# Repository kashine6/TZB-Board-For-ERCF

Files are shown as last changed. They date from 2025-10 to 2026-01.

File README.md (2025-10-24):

# TZB V1 Mainboard Manual

English | [中文](README_CN.md)

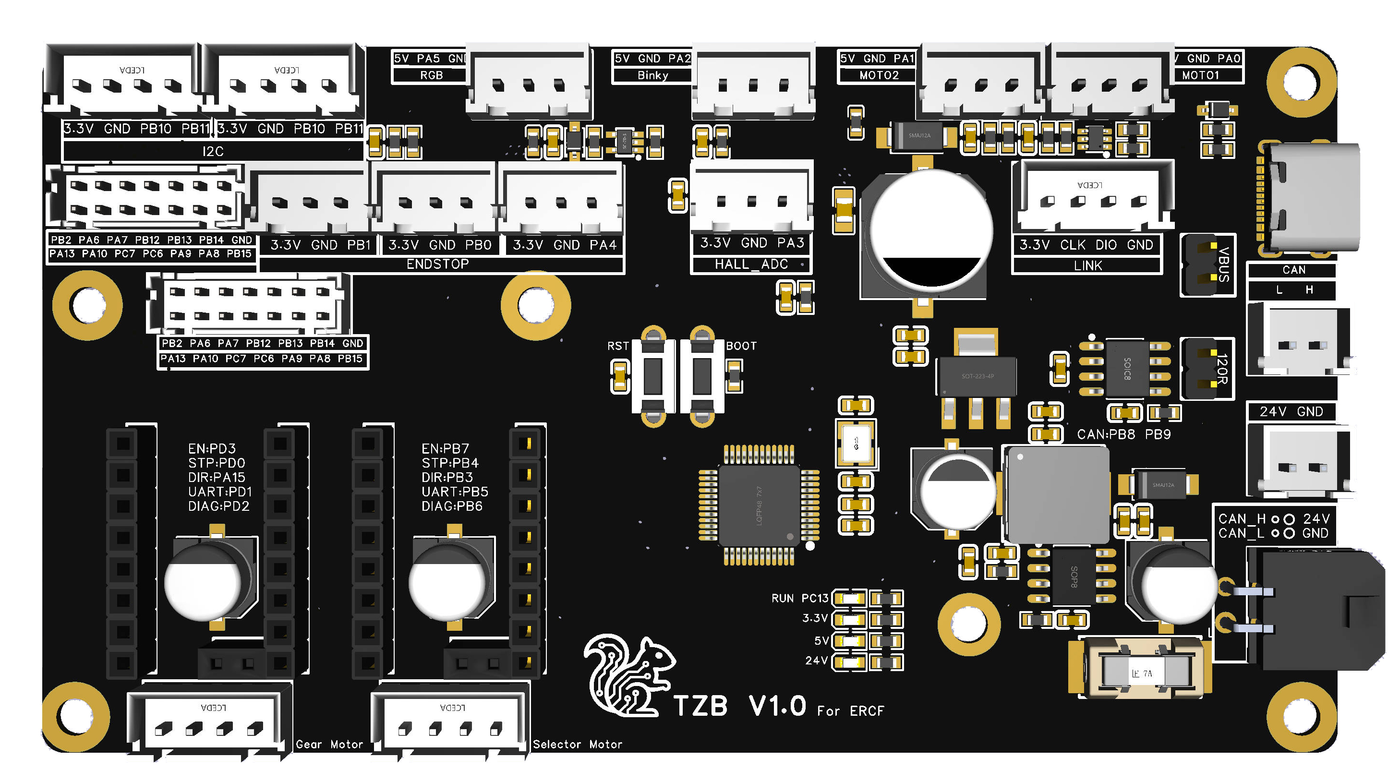
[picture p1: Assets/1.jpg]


---

## Table of Contents

- [1. Introduction](#1-introduction)
- [2. PIN Diagram](#2-pin-diagram)
- [3. Flashing Guide](#3-flashing-guide)
  - [3.1. Flashing Katapult (Optional)](#31-flashing-katapult-optional)
  - [3.2. Compiling Klipper Firmware](#32-compiling-klipper-firmware)
  - [3.3. Updating Firmware via Katapult](#33-updating-firmware-via-katapult)
  - [3.4. Updating Firmware via DFU](#34-updating-firmware-via-dfu)
- [4. ERCF Wiring Diagram](#4-ercf-wiring-diagram)
- [5. Happy Hare Software Configuration](#5-happy-hare-software-configuration)
- [6. I2C Temperature and Humidity Configuration](#6-i2c-temperature-and-humidity-configuration)

---

## 1. Introduction

The **TZB V1 Mainboard** is a dedicated mainboard developed for the ERCF.

It has the following features:

- Main chip uses STM32G0B1CBT6 MCU
- Supports both USB serial and CAN interface connections
- 2 stepper motor slots based on TMC2209 in UART mode, supporting sensorless homing (Diag)
- The 5V interface can provide a large current of 5A, with optimized inductor and capacitor heat dissipation to ensure sufficient and stable power for servos and LEDs
- Two mirrored 2x7P XHD2.0 connectors, convenient for paralleling the two sets of microswitches in ERCF V3, simplifying wiring
- All silkscreen labels are on the front for ease of use
- 1 x RGB LED connector
- 2 x Servo connectors, capable of driving a remote cutters
- 1 x Binky encoder connector
- 16 x Microswitch control connectors, which can support up to a 16-color ERCF if fully utilized
- 1 x I2C interface, using a hardware I2C port, which can be used to connect a temperature and humidity sensor
- 1 x 24V GND connector, which can be used to supply power to remote cutters that require more than 5V
- 1 x External CAN connector, which can be used to connect other mainboards, such as a passive enclosure mainboard
- 1 x ADC interface, for use with a proportional filament sync feedback sensor using an analog Hall effect sensor

## 2. PIN Diagram

The wiring diagram for this mainboard is entirely on the front, making it clear at a glance without needing a separate pinout diagram.



## 3. Flashing Guide

### 3.1 Flashing Katapult (Optional)

Users who only use a CAN connection and want the convenience of quick firmware updates by pressing the Reset button can choose to flash Katapult (formerly known as Canboot).

Katapult is not mandatory, regardless of whether you use a CAN or USB connection.

```bash
# Go to the home directory
cd ~
 
# Download katapult (skip if you already have it)
git clone https://github.com/Arksine/katapult
 
# Enter the katapult directory
cd katapult
```

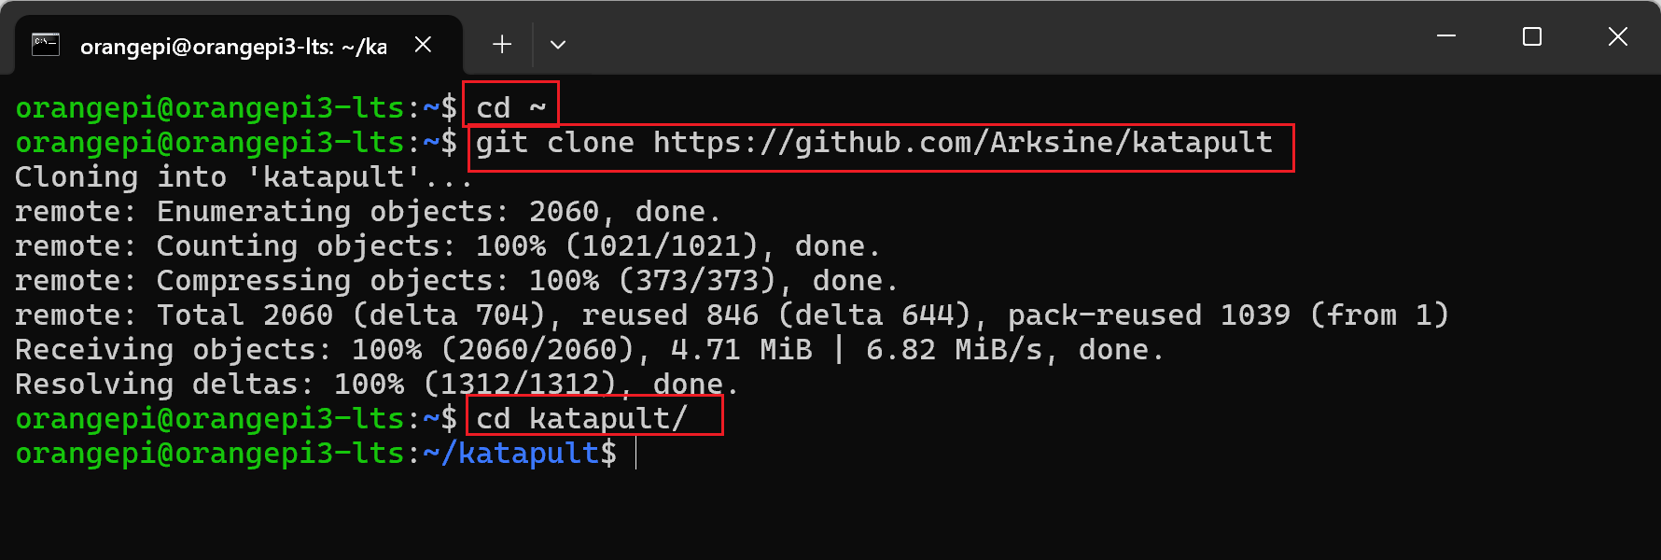
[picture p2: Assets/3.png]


```bash
# Clean the previous build
make clean
 
# Modify the build configuration, fill in the parameters as shown in the image below
make menuconfig
 
# After verifying the settings, press q to exit, select y, then type make to start compiling
make
```

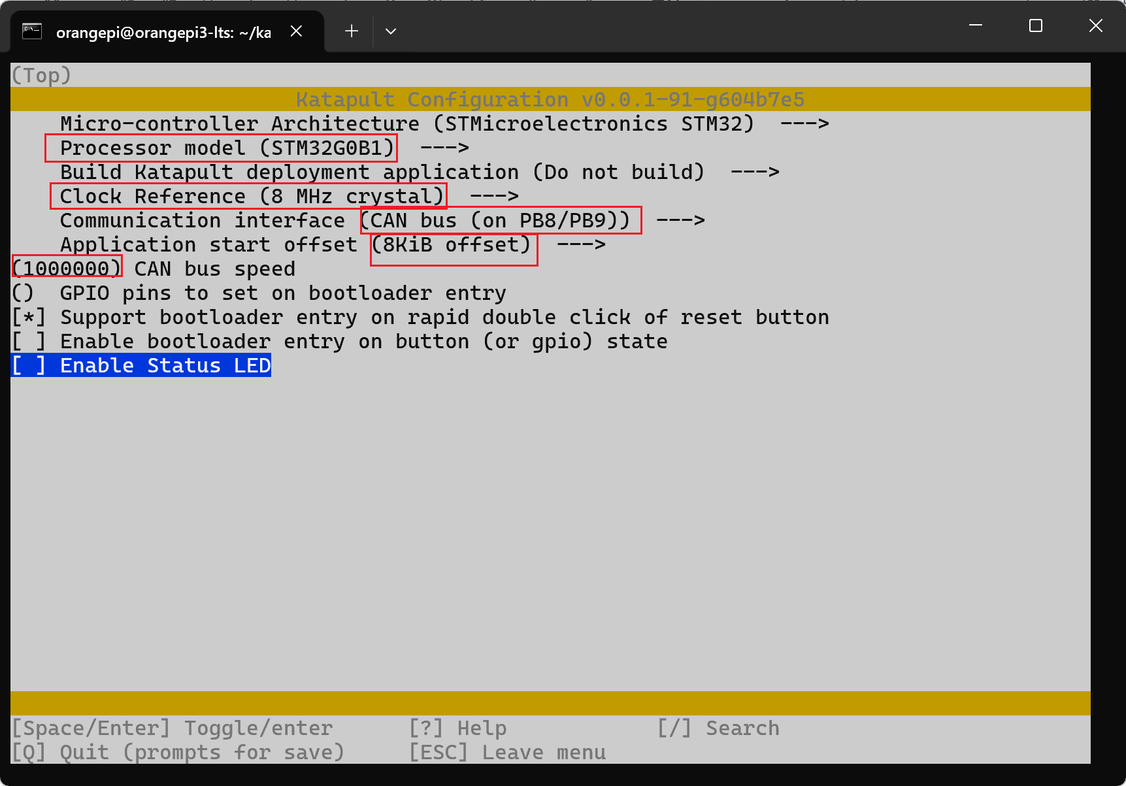
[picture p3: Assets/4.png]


> [!TIP]
> The speed can be set according to your needs, 1000000 is recommended.

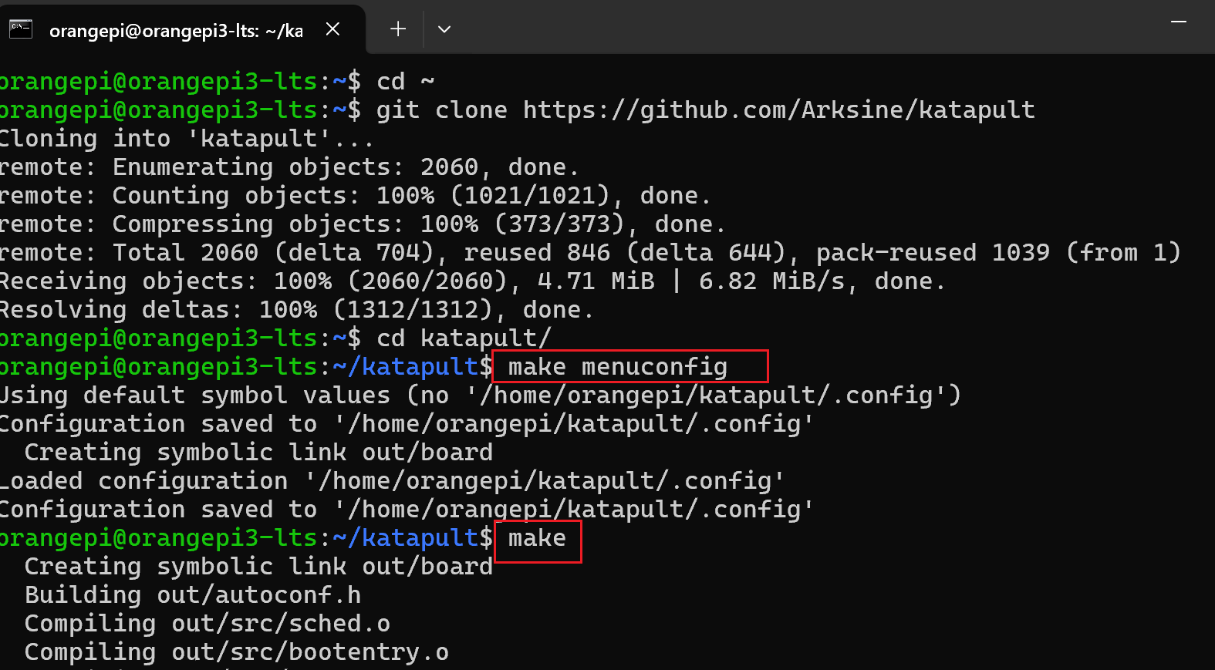
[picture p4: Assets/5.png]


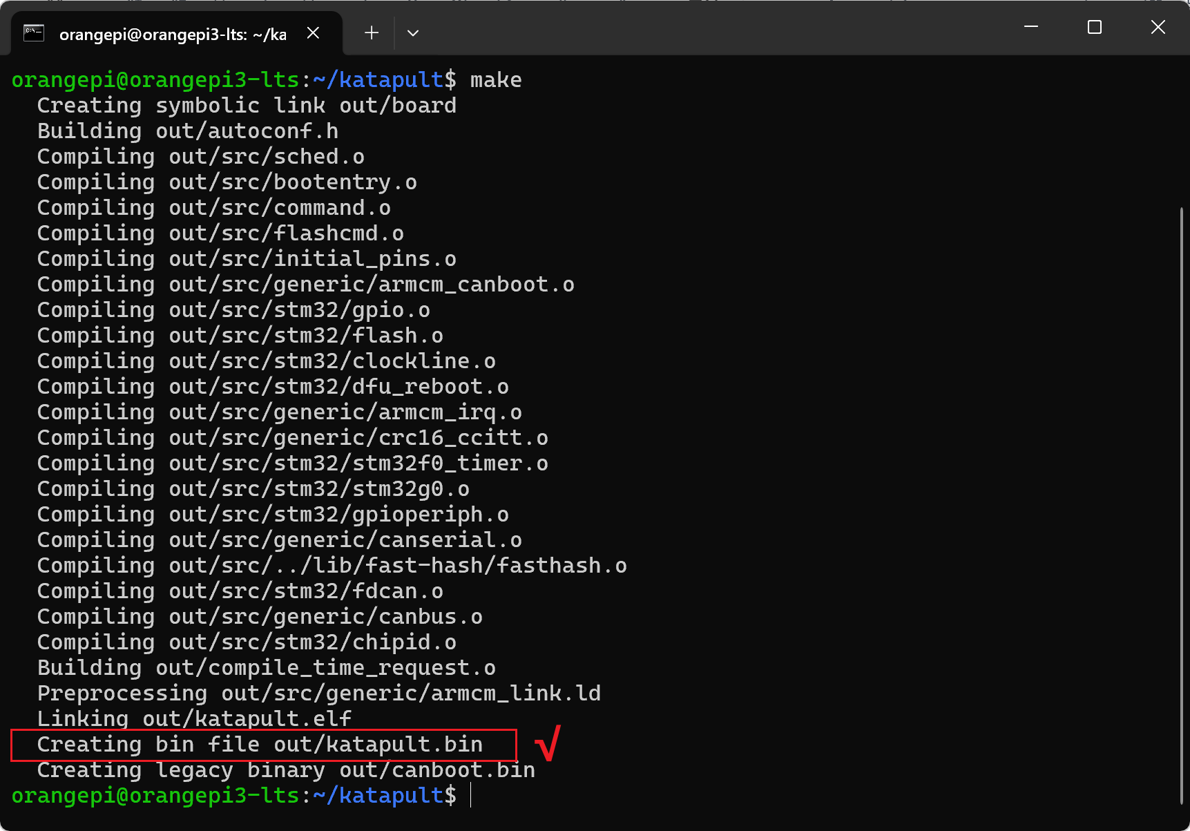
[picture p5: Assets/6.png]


After compilation, katapult.bin will be generated in the ~/katapult/out folder.

**Entering DFU Mode**

Use a jumper to short the 5V USB pins. After shorting, you can power the board via USB for flashing. 

> [!TIP]
> Remember to remove the jumper after flashing is complete.  

If you are using 24V to power the board, you do not need to short the jumper, but you can only use Method 2 below to enter DFU mode.

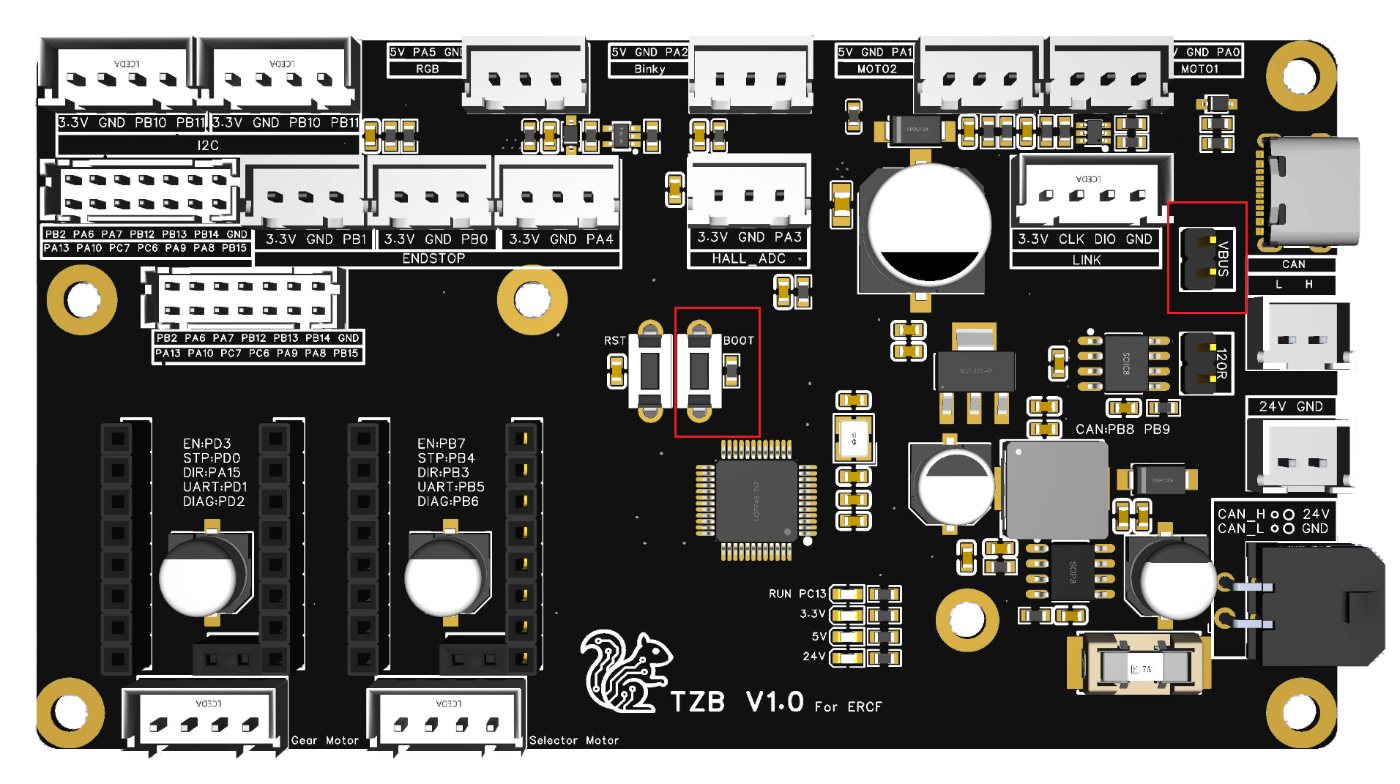
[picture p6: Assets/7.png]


- **Method 1 to enter DFU:** With the board completely powered off, press and hold the Boot button, connect the board to the host computer with a Type-C cable, then release the Boot button.

- **Method 2 to enter DFU:** If the board is powered on, connect it to the host computer with a Type-C cable, then press and hold the Boot button, press and release the Reset button, release the Reset button, and finally release the Boot button.

Then use the lsusb command to check if a DFU device is present.

```bash
lsusb
```

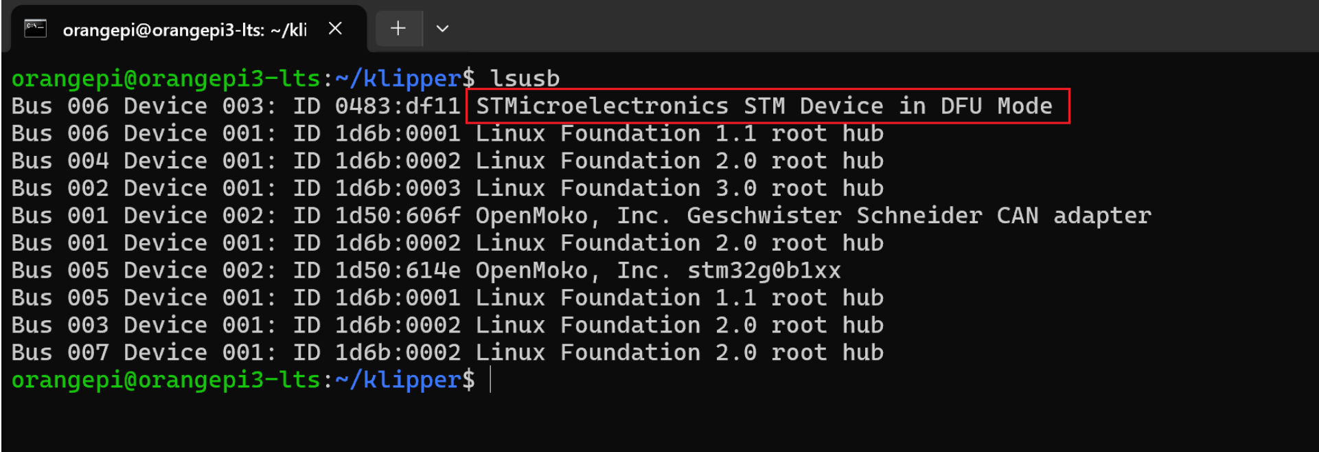
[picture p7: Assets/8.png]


Use the following command to flash the board:

```bash
make flash FLASH_DEVICE=0483:df11
```

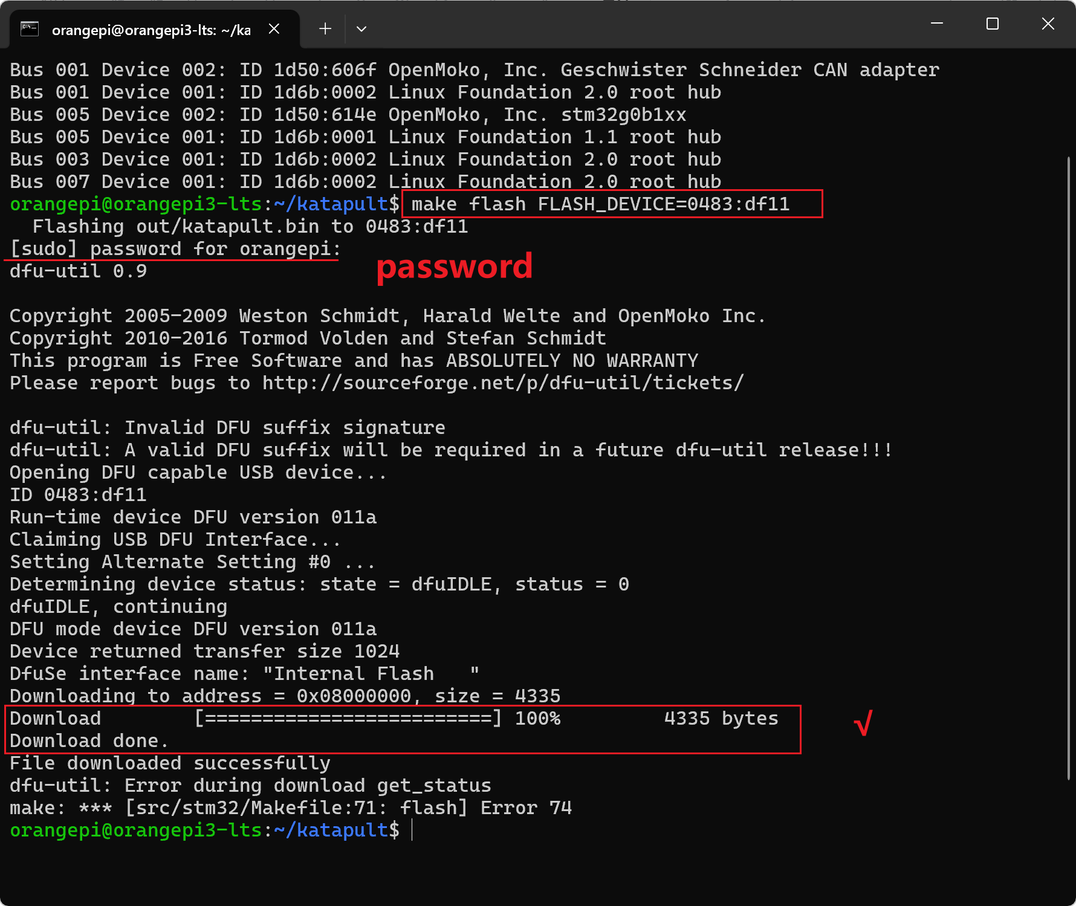
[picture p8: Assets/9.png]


After flashing is complete, please unplug the USB cable and connect the CAN signal cable and 24V power supply.

> [!NOTE]
> 1: Remember to remove the 5V USB jumper.  
> 2: If you have multiple CAN devices, you only need to short the 120-ohm resistor on one device. It is best to short the 120-ohm resistor on the mainboard at the end of the chain.  
> 3: Pay close attention to the wiring order of 24V, GND, CAN-H, and CAN-L. Double-check carefully. Incorrect wiring may cause the mainboard to burn out, and you will be responsible for the consequences.  

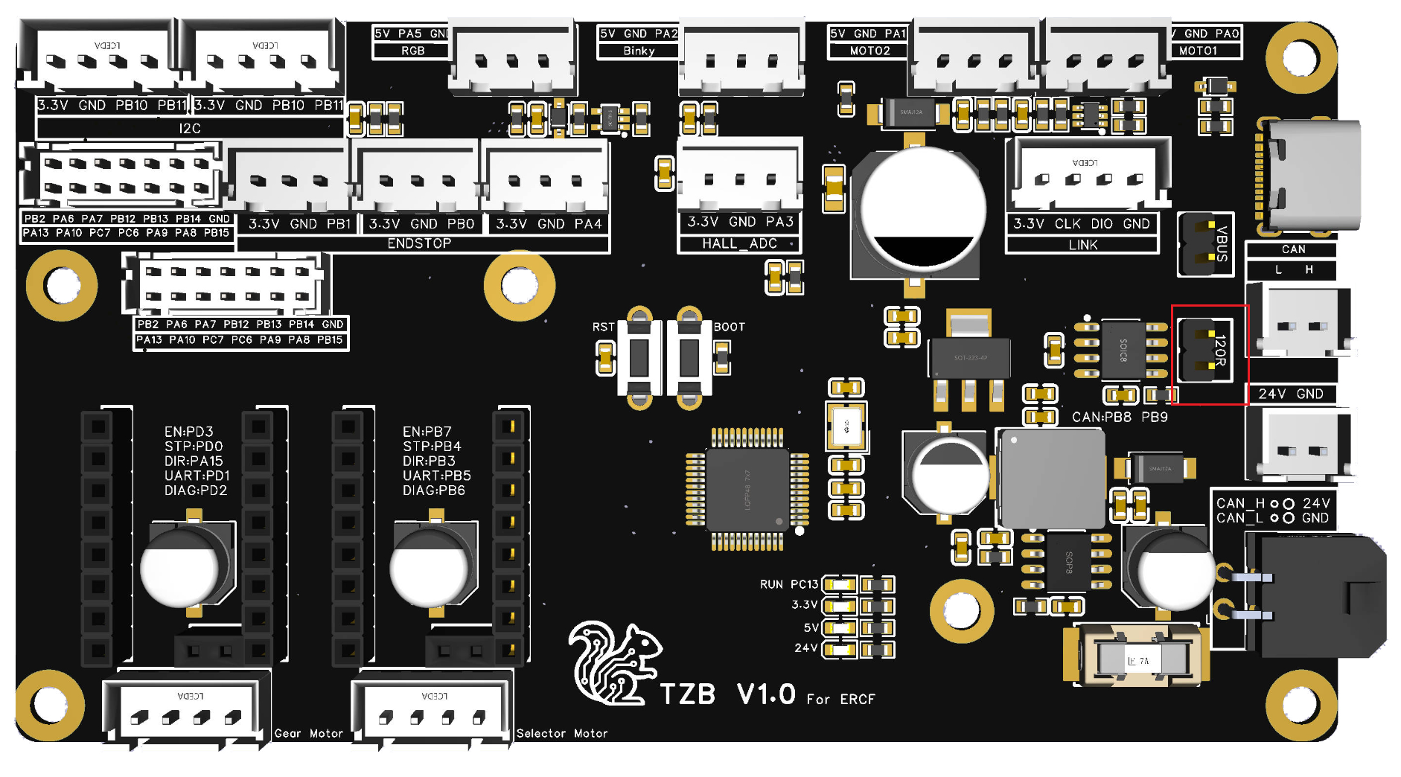
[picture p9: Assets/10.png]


Use the following command to check the CAN UUID. 
> [!TIP]
> You may need to quickly double-press the reset button to enter the bootloader.

```bash
~/klippy-env/bin/python ~/klipper/scripts/canbus_query.py can0
```

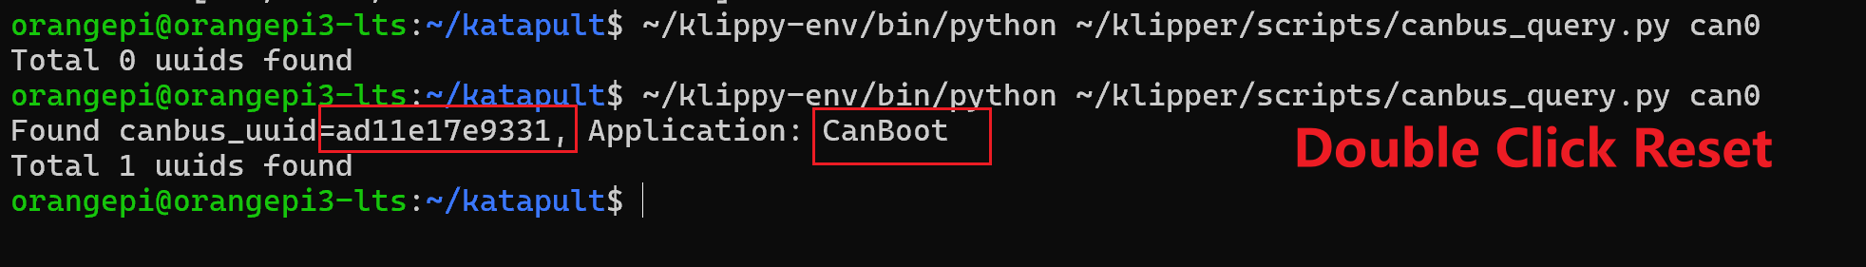
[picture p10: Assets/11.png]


### 3.2 Compiling Klipper Firmware

SSH into your host machine.

```bash
# cd to the klipper directory
cd ~/klipper
 
# Clean the previous build
make clean
 
# Configure the build parameters [refer to the image below]
make menuconfig
```



Set the build parameters according to the protocol you need to use.

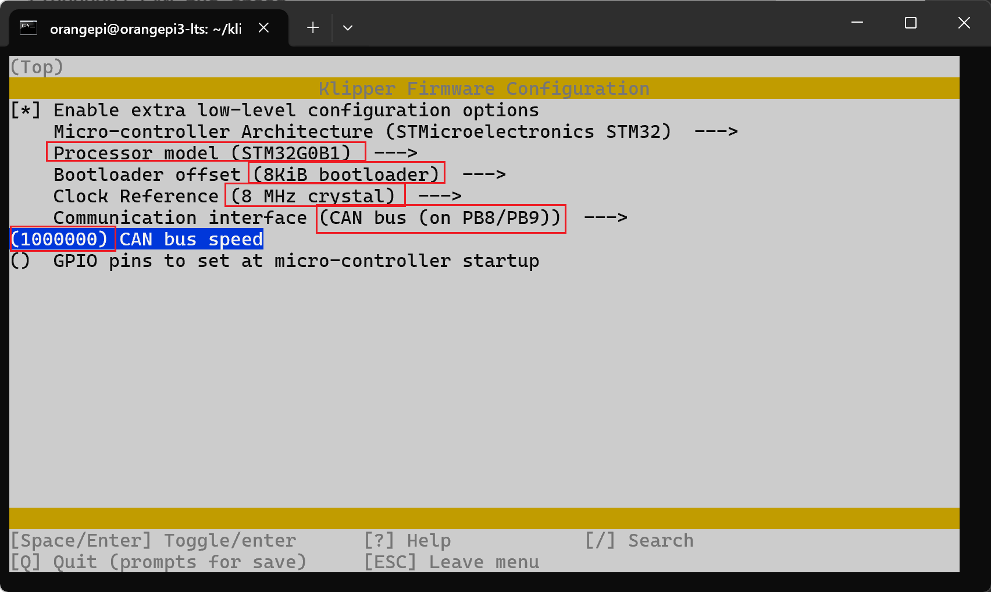
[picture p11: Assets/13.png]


```bash
# If not using Katapult
Bootloader offset (No bootloader) --->
 
# If using Katapult
Bootloader offset (8KiB bootloader) --->
 
# If using USB communication via Type-C
Communication interface (USB (on PA11/PA12)) --->
 
# If using CANBus communication
Communication interface (CAN bus (on PD0/PD1)) --->
 (1000000) CAN bus speed
```

Press `q` to exit, and `y` to save.

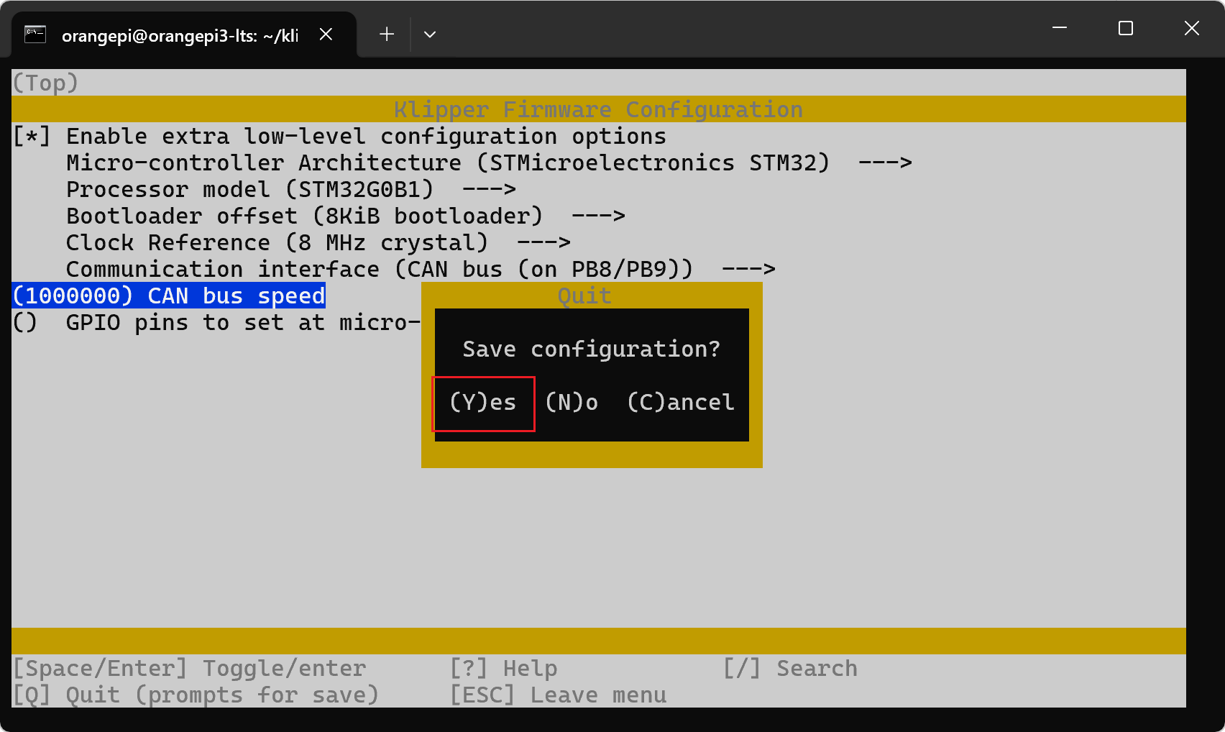
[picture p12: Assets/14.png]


Enter the make command to start compiling.

```bash
make
```

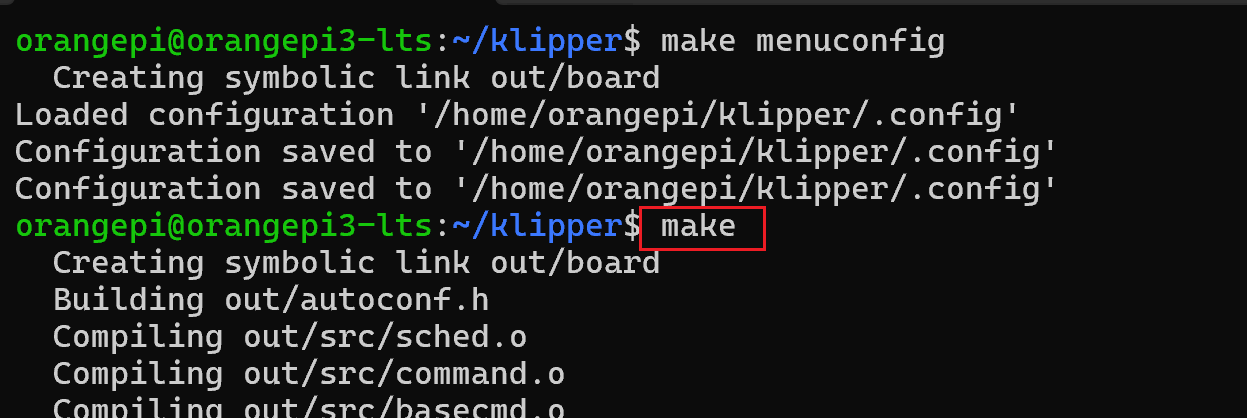
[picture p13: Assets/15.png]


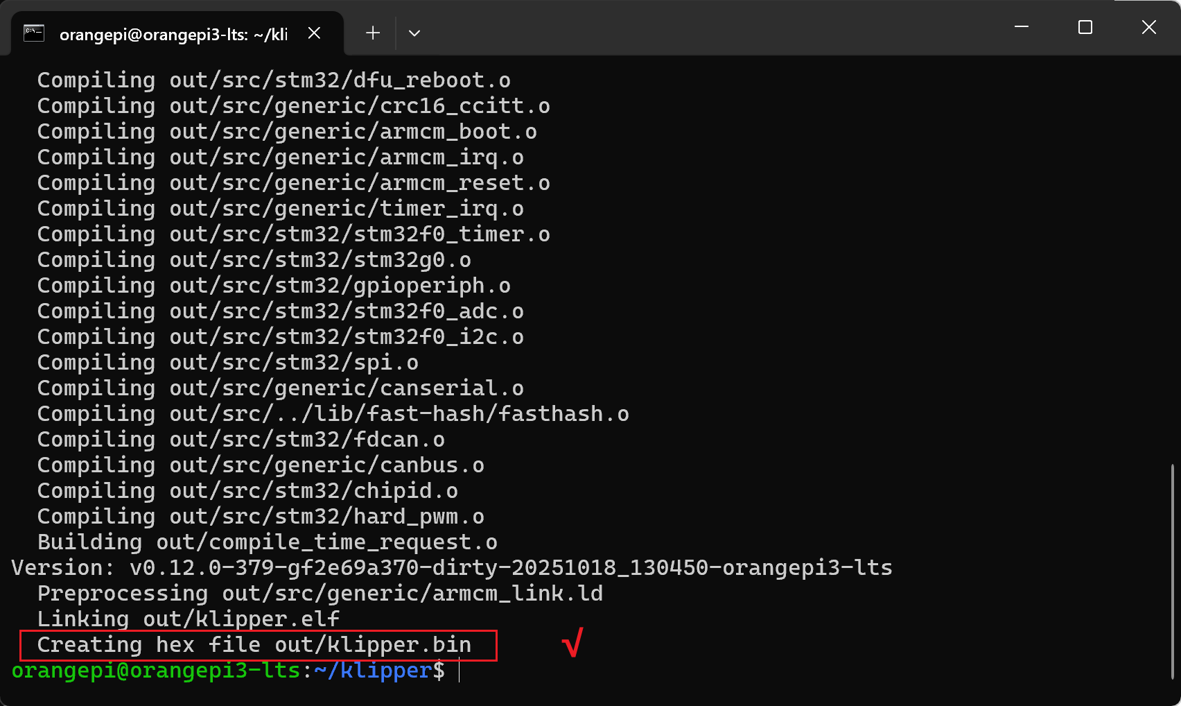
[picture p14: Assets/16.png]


### 3.3 Updating Firmware via Katapult

Connect the CAN signal cable and 24V power supply.

> [!NOTE]
> 1: Remember to remove the 5V USB jumper.  
> 2: If you have multiple CAN devices, you only need to short the 120-ohm resistor on one device.  
> 3: Pay close attention to the wiring order of 24V, GND, CAN-H, and CAN-L. Double-check carefully. Incorrect wiring may cause the mainboard to burn out, and you will be responsible for the consequences.  



Then use the following command to check the UUID:

```bash
~/klippy-env/bin/python ~/klipper/scripts/canbus_query.py can0
```

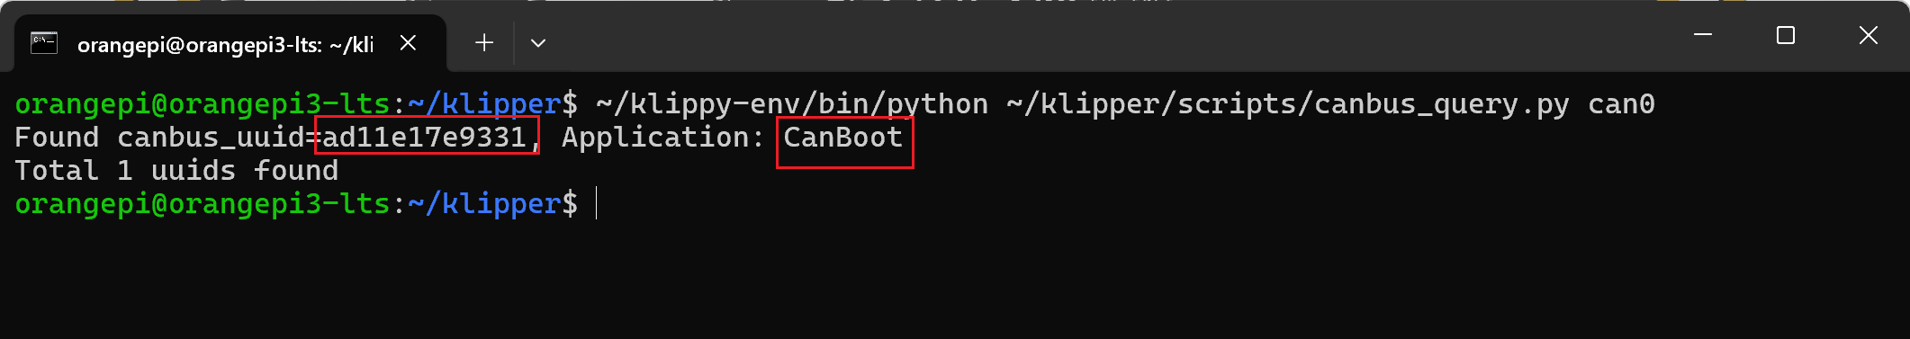
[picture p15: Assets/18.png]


Use the following command to flash in CAN mode:

```bash
cd ~/katapult/scripts
 
python3 flashtool.py -i can0 -f ~/klipper/out/klipper.bin -u your_uuid_here
```

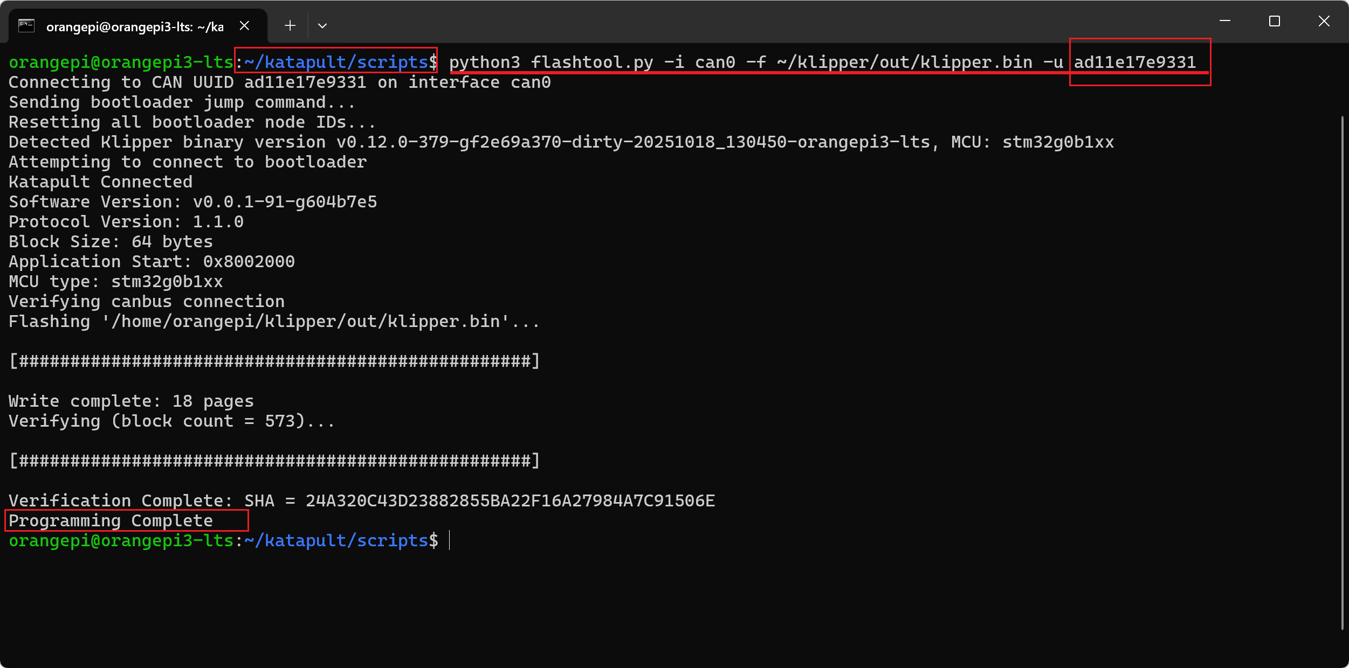
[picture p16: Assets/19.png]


Then continue to use the previous command to check the CAN information.



> [!TIP]
> To upgrade the CAN firmware in the future, repeat this process. When compiling the Katapult firmware earlier, we set it to enter Katapult mode by double-pressing the reset button. 
> In practice, you can also directly enter the flashing command, and the board will automatically restart and enter Katapult.  

### 3.4 Updating Firmware via DFU

1: Enter DFU mode.

Use a jumper to short the 5V USB pins. After shorting, you can power the board via USB for flashing. 

> [!TIP]
> Remember to remove the jumper after flashing is complete.

If you are using 24V to power the board, you do not need to short the jumper, but you can only use Method 2 below to enter DFU mode.

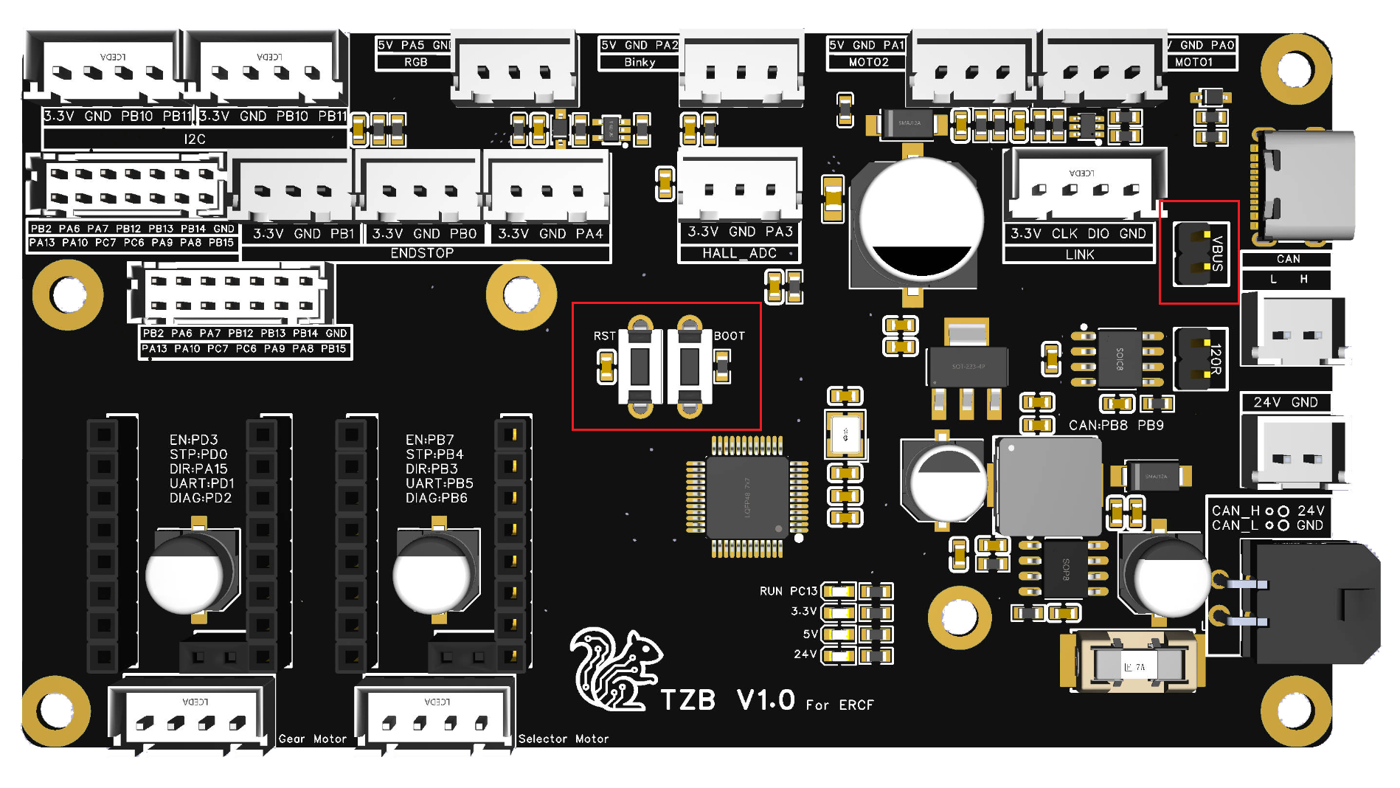
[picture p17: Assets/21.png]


- Method 1 to enter DFU: With the board completely powered off, press and hold the Boot button, connect the board to the host computer with a Type-C cable, then release the Boot button.

- Method 2 to enter DFU: If the board is powered on, connect it to the host computer with a Type-C cable, then press and hold the Boot button, press and release the Reset button, release the Reset button, and finally release the Boot button.

2: In SSH, type lsusb to check if a DFU device appears. Normally, a DFU device should appear.

If no DFU device appears, repeat the operation.

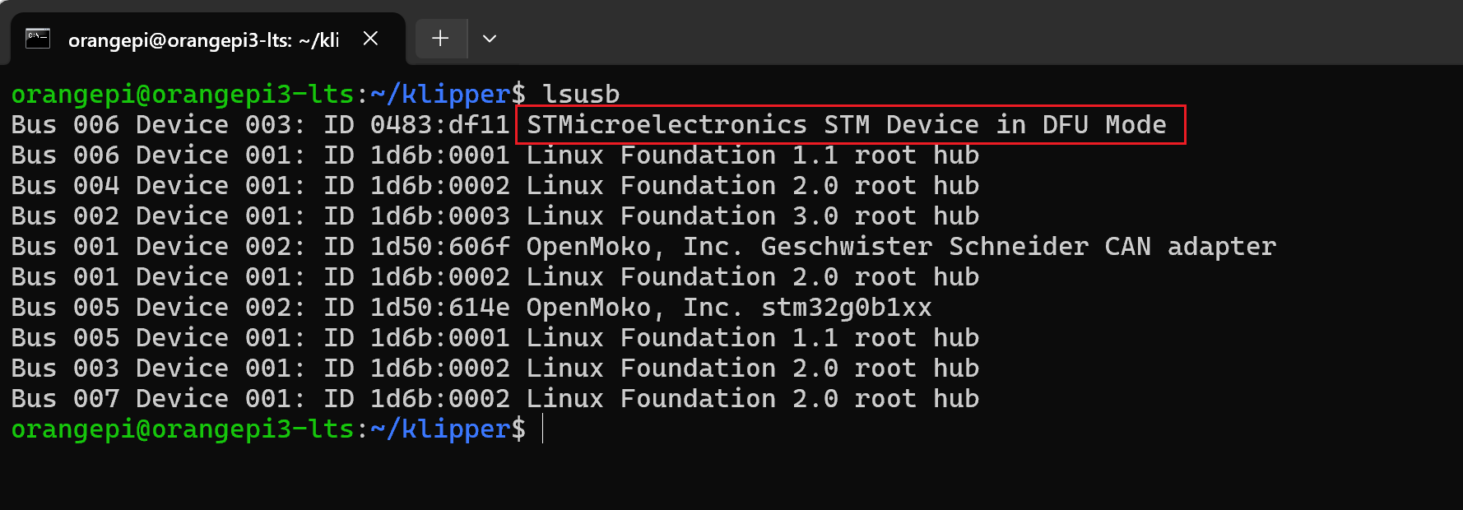
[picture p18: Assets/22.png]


3: In SSH, enter:

```bash
# Make sure you are in the klipper directory
cd ~/klipper
 
# 0483:df11 is the ID found with lsusb earlier
# If it says make not found, install it with sudo apt install dfu-util -y
 
make flash FLASH_DEVICE=0483:df11
```

The flashing process will then begin [you may need to enter your password]. Wait for the progress bar to complete. When "successfully" appears, it means the flashing was successful.

You can ignore any errors that appear after "successfully".

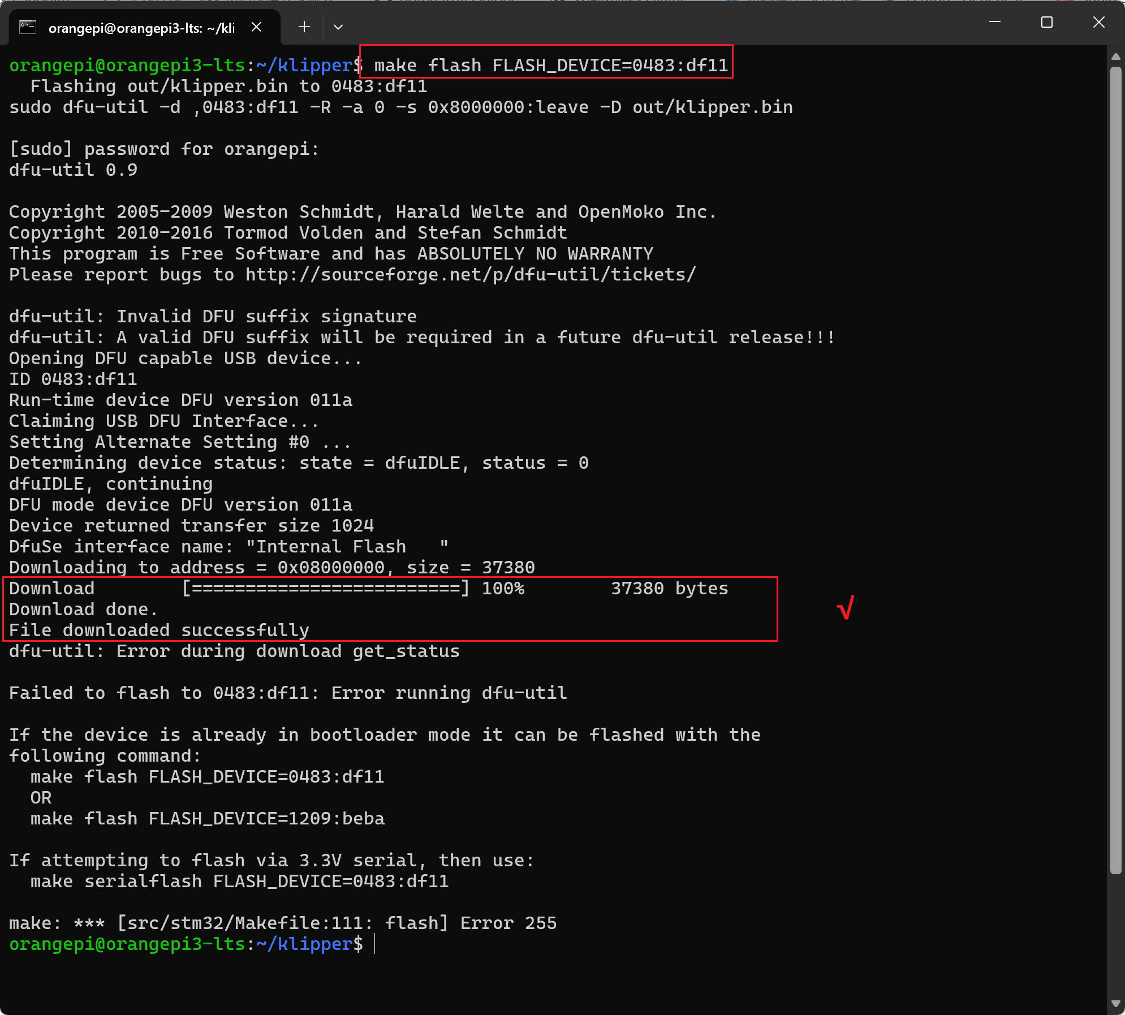
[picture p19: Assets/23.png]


Flashing is complete.

4: **Get the serial ID**

Unplug and replug the USB data cable, use lsusb to check if there is an stm32f446 device.

Use the following command to check the device's serial ID:

```bash
ls /dev/serial/by-id/
```



The serial ID for this device is:

```bash
serial: /dev/serial/by-id/usb-Klipper_stm32g0b1xx_20003A00025030544E383020-if00
```

> [!TIP]
> For later use, please remove the 5V USB jumper and connect 24V power to the CAN interface.

## 4. ERCF Wiring Diagram

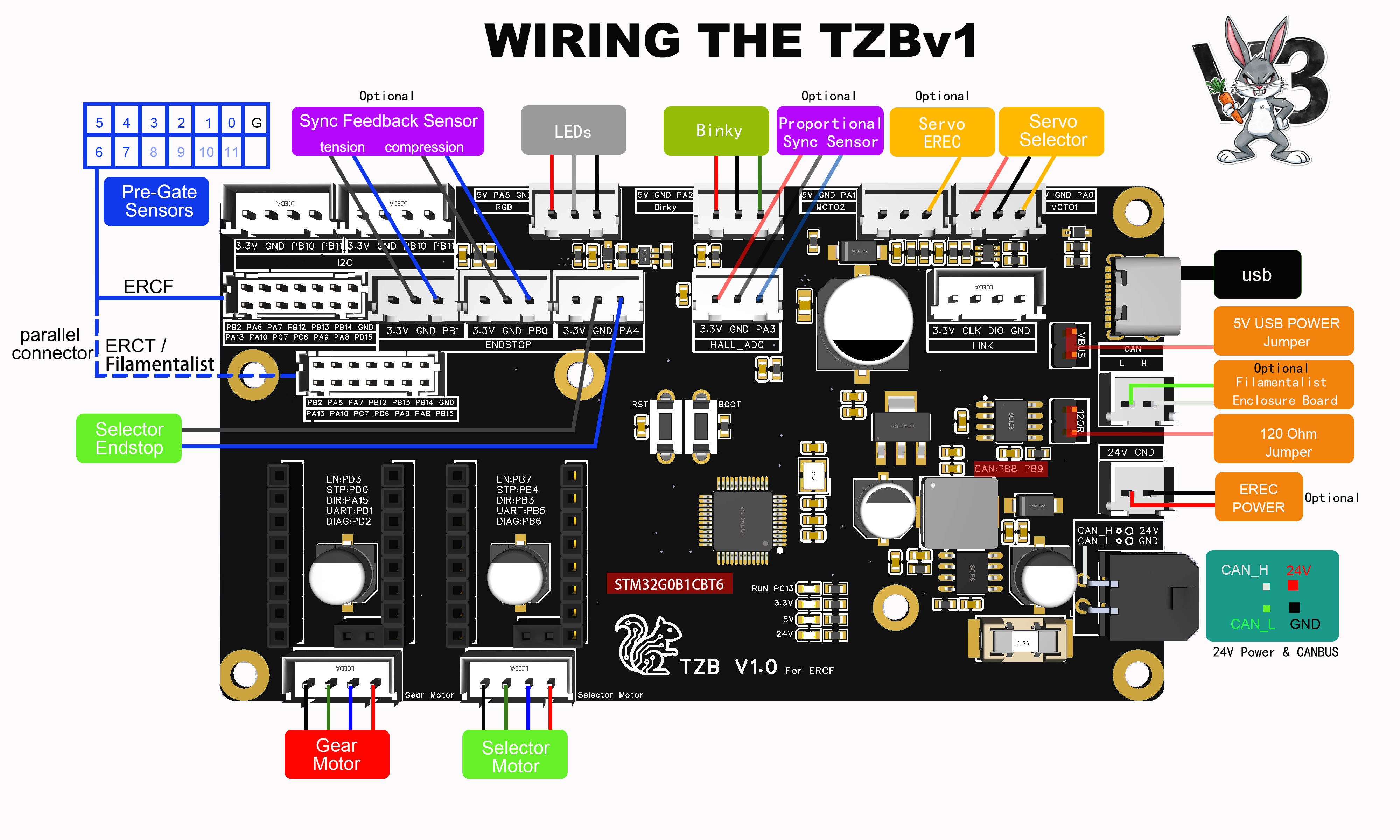
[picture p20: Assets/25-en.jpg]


## 5. Happy Hare Software Configuration

> [!TIP]
> For all microswitch inputs, you need to add the pull-up symbol "^" before the PIN.  
> Binky does not require it.  

After installation, you need to go to the mmu/base/mmu.cfg file to modify the pin-related content. Copy the content below and overwrite the corresponding section [compatible with HH3.2 and above versions].

HappyHare adaptation is in progress.

```Python
#TZB V1.0
[board_pins mmu]
mcu: mmu # Assumes using an external / extra mcu dedicated to MMU
aliases:
    MMU_GEAR_UART=PD1,
    MMU_GEAR_STEP=PD0,
    MMU_GEAR_DIR=PA15,
    MMU_GEAR_ENABLE=PD3,
    MMU_GEAR_DIAG=PD2,

    MMU_GEAR_UART_1=,
    MMU_GEAR_STEP_1=,
    MMU_GEAR_DIR_1=,
    MMU_GEAR_ENABLE_1=,
    MMU_GEAR_DIAG_1=,

    MMU_GEAR_UART_2=,
    MMU_GEAR_STEP_2=,
    MMU_GEAR_DIR_2=,
    MMU_GEAR_ENABLE_2=,
    MMU_GEAR_DIAG_2=,

    MMU_GEAR_UART_3=,
    MMU_GEAR_STEP_3=,
    MMU_GEAR_DIR_3=,
    MMU_GEAR_ENABLE_3=,
    MMU_GEAR_DIAG_3=,

    MMU_SEL_UART=PB5,
    MMU_SEL_STEP=PB4,
    MMU_SEL_DIR=PB3,
    MMU_SEL_ENABLE=PB7,
    MMU_SEL_DIAG=PB6,
    MMU_SEL_ENDSTOP=PA4,
    MMU_SEL_SERVO=PA0,

    MMU_ENCODER=PA2,
    MMU_GATE_SENSOR=,
    MMU_NEOPIXEL=PA5,

    MMU_PRE_GATE_0=PB14,
    MMU_PRE_GATE_1=PB13,
    MMU_PRE_GATE_2=PB12,
    MMU_PRE_GATE_3=PA7,
    MMU_PRE_GATE_4=PA6,
    MMU_PRE_GATE_5=PB2,
    MMU_PRE_GATE_6=PA13,
    MMU_PRE_GATE_7=PA10,
    MMU_PRE_GATE_8=PC7,
    MMU_PRE_GATE_9=PC6,
    MMU_PRE_GATE_10=PA9,
    MMU_PRE_GATE_11=PA8,

    MMU_POST_GEAR_0=,
    MMU_POST_GEAR_1=,
    MMU_POST_GEAR_2=,
    MMU_POST_GEAR_3=,
    MMU_POST_GEAR_4=,
    MMU_POST_GEAR_5=,
    MMU_POST_GEAR_6=,
    MMU_POST_GEAR_7=,
    MMU_POST_GEAR_8=,
    MMU_POST_GEAR_9=,
    MMU_POST_GEAR_10=,
    MMU_POST_GEAR_11=,

    MMU_ESPOOLER_RWD_0={espooler_rwd_0_pin},
    MMU_ESPOOLER_FWD_0={espooler_fwd_0_pin},
    MMU_ESPOOLER_EN_0={espooler_en_0_pin},
    MMU_ESPOOLER_TRIG_0=,
    MMU_ESPOOLER_RWD_1={espooler_rwd_1_pin},
    MMU_ESPOOLER_FWD_1={espooler_fwd_1_pin},
    MMU_ESPOOLER_EN_1={espooler_en_1_pin},
    MMU_ESPOOLER_TRIG_1=,
    MMU_ESPOOLER_RWD_2={espooler_rwd_2_pin},
    MMU_ESPOOLER_FWD_2={espooler_fwd_2_pin},
    MMU_ESPOOLER_EN_2={espooler_en_2_pin},
    MMU_ESPOOLER_TRIG_2=,
    MMU_ESPOOLER_RWD_3={espooler_rwd_3_pin},
    MMU_ESPOOLER_FWD_3={espooler_fwd_3_pin},
    MMU_ESPOOLER_EN_3={espooler_en_3_pin},
    MMU_ESPOOLER_TRIG_3=,
```

## 6. I2C Temperature and Humidity Configuration

If you want to connect an I2C temperature and humidity sensor, using BME280 as an example, you can set it up as follows.

This configuration will use hardware I2C, thus saving processor resources.

```Python
[temperature_sensor MMU_enclosure]
sensor_type: BME280
i2c_mcu: mmu
i2c_bus: i2c2_PB10_PB11
i2c_address: 118
```

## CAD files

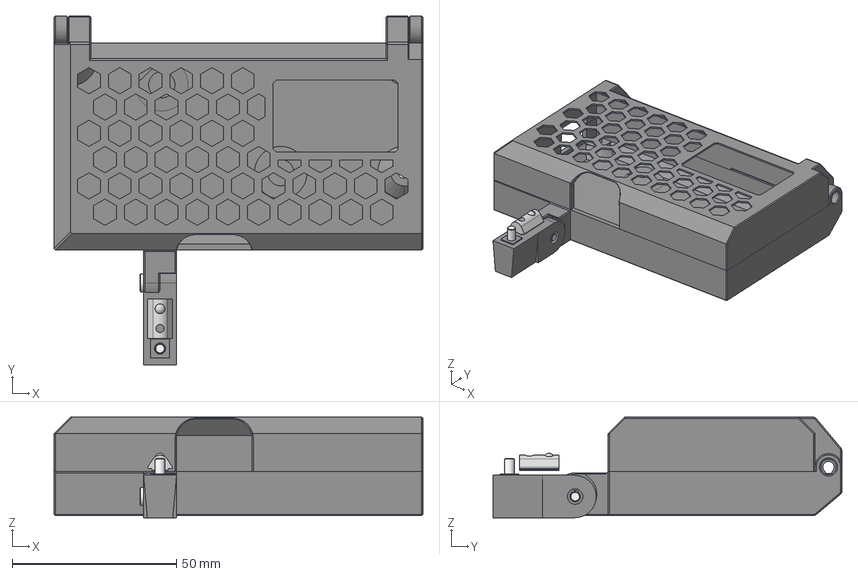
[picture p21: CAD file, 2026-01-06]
3D/ERCF_V3_TZBV1_Box.step
112.3 x 106.2 x 30.7 mm
Base.stl
_Fasteners (10)
Lid.stl
_Fasteners (11)
M3 Roll-in Nut
M3x8 SHCS x 2

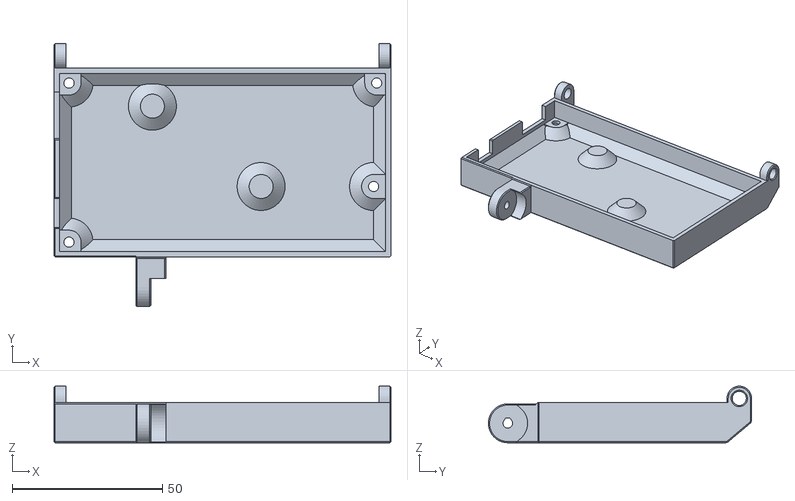
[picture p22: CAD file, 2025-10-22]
Electronics_Box_For_ERCF/TZBv1_Box_Base_v01.stl
112.3 x 87.7 x 18.9

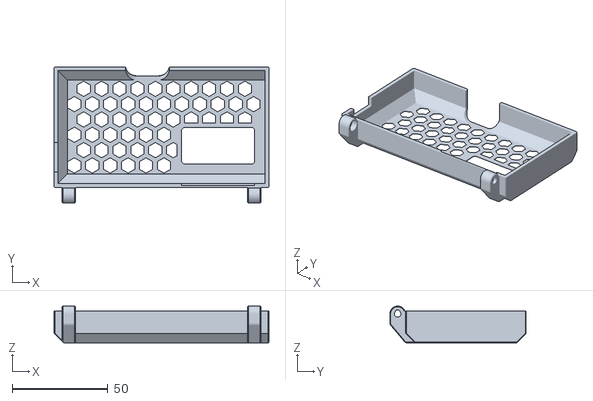
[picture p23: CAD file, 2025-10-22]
Electronics_Box_For_ERCF/TZBv1_Box_Lid_v01.stl
112.3 x 71.2 x 19.3

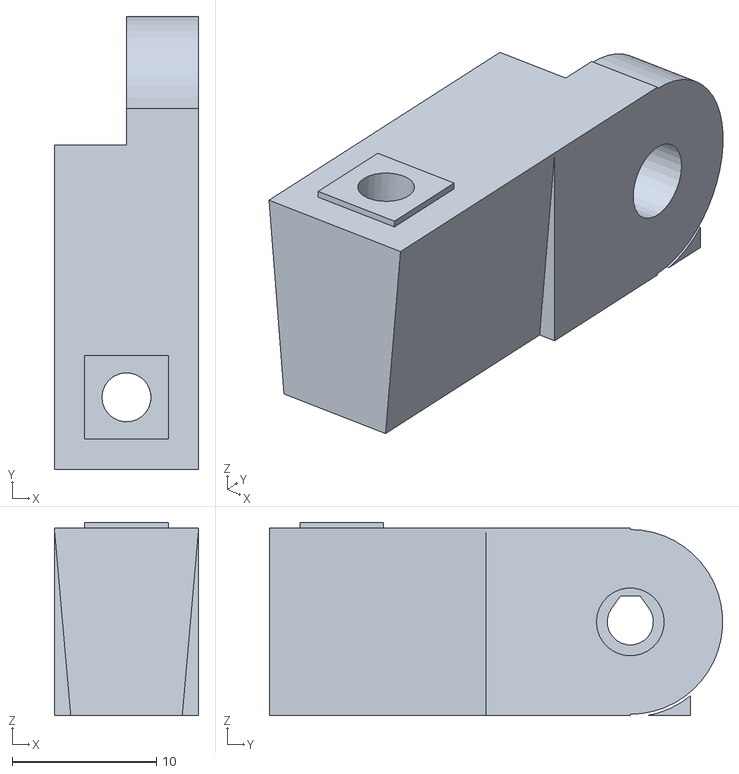
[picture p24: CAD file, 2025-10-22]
Electronics_Box_For_ERCF/Mount_hinge_90_v03.stl
10.00 x 31.4 x 13.4

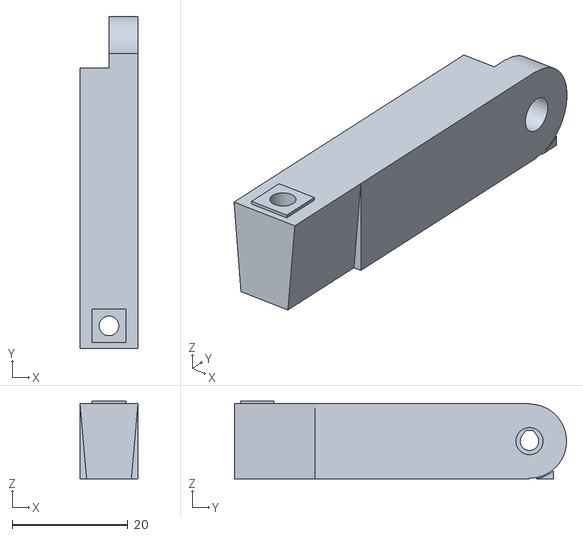
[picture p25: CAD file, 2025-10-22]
Electronics_Box_For_ERCF/Mount_hinge_long_90_v01.stl
10.0 x 57.3 x 13.4
